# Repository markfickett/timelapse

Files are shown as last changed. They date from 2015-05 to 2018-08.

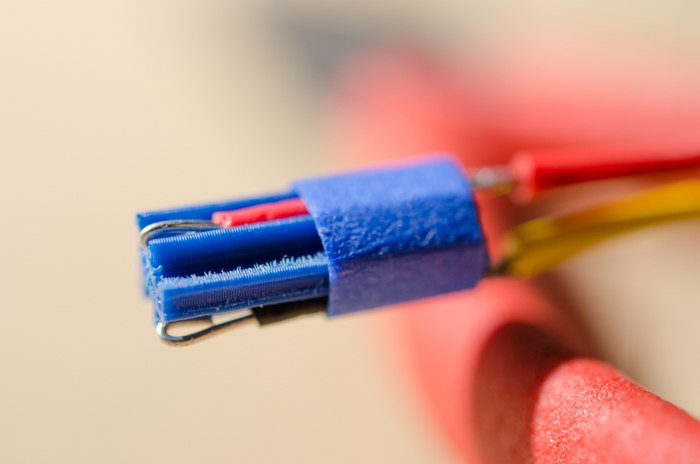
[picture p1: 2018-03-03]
nikond90acplug/151021nikond90acplugendside.jpg

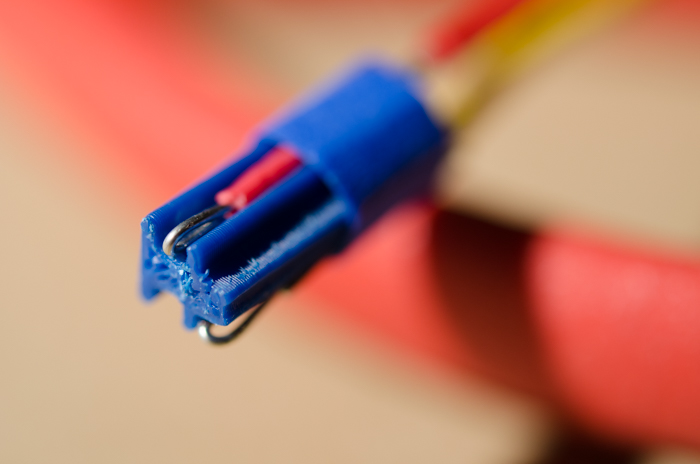
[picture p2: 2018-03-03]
nikond90acplug/151021nikond90acplugendquarter.jpg

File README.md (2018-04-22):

# Outdoor Battery Powered dSLR Time Lapse

## Parts

This is based around a dSLR for the high-quality image sensor and lenses. A Nikon D90 costs around $200 used in 2015, and has connections for a wired remote and external power supply.

### Control board

The control board is Arduino-based, using a bare ATMega328p, with a MOSFET to control camera power and an opto-isolater to control camera exposure.

#### Components

Many of these parts may be found cheaper at Mouser or DigiKey, but SparkFun or Adafruit makes finding the right component and learning to use it easy.

 * ATMega328p [$6 from Sparkfun](https://www.sparkfun.com/products/10524) and 28-DIP socket [$1 from SparkFun](https://www.sparkfun.com/products/7942).
 * optoisolator (2+ channel) [$2 from Mouser](http://www.mouser.com/ProductDetail/Vishay-Semiconductors/ILD2/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)
 * Chrono Dot real time clock module [$20 from Adafruit](https://www.adafruit.com/products/255)
 * MOSFET [$1 from Sparkfun](https://www.sparkfun.com/products/10213) for camera power control
 * NPN transistor [$1 from Sparkfun](https://www.sparkfun.com/products/521) for LED display power control
 * photoresistor (CdS) [$1 from Adafruit](http://www.adafruit.com/product/161), to sense the camera's activity LED and ambient light levels
 * 5V 1A buck converter for regulated power [$15 from Adafruit](https://www.adafruit.com/product/1065). Idle current of under 2mA.
 * Small tactile switches [$5 for 20 from Adafruit](https://www.adafruit.com/product/1489) for a reset and debug buttons.
 * I2C 7-segment display [$20 from Adafruit](https://www.adafruit.com/product/878), though I might go for the [alphanumeric version](https://www.adafruit.com/product/1911) were I starting again.
 * assorted resistors
 * 22 uF electrolytic capacitor for filtering

I used [SparkFun's $20 Tiny AVR Programmer](https://www.sparkfun.com/products/11801) to [upload to the bare ATMega328](https://www.sparkfun.com/products/11801#comment-561f19cbce395f7a0d8b4567). I soldered [female headers](https://www.adafruit.com/product/598) on the programmer, and used Adafruit's [$4 female-female jumpers](https://www.adafruit.com/product/266) along with [extra-long headers](https://www.adafruit.com/product/400) to jump to the ISP header on the board.

#### Circuit

See the `eagle/` subdirectory for circuit and PCB details including [schematic PDF](eagle/timelapse.sch.pdf).

I designed PCBs using EAGLE's non-commercial free license and autolayout, following [SparkFun's tutorial](https://learn.sparkfun.com/tutorials/using-eagle-schematic), and had them printed by [OSH Park](https://oshpark.com/).

### Off-Board Parts and Connectors

 * 12v to 9v DC regulator [$8 on Amazon](http://www.amazon.com/gp/product/B00A71E52G) for power to camera (draws 12mA @ 12v with no load)
 * AC adapter plug (3D printed plug for Nikon D90; [photo](nikond90acplug/151021nikond90acplugendquarter.jpg), [STL file](nikond90acplug/NikonD90AcPlugReducedH.stl), [Thingiverse](https://www.thingiverse.com/thing:1107374/apps/print/))
 * XT60s (power connections, [$2 from Sparkfun](https://www.sparkfun.com/products/10474), compare at HobbyKing)
 * servo cables (peripheral/control connections)
 * lamp cord (battery connection)
 * wired dSLR remote [$6 MC-DC2 clone on Amazon](http://www.amazon.com/gp/product/B003JR8GCU)

### Hardware

A Pelican case provides a sturdy, watertight enclosure which is easy to open and close; and the fins on the hinge side facilitate mounting.

 * Pelican case 1300 NF ($60 on eBay)
 * glass (from a small thrift-store picture frame; attached with JB weld)
 * silica gel (dried and reused)
 * treated wood and screws for mounting
 * 5W solar panel ([$35 on Amazon](https://www.amazon.com/gp/product/B004FOEUI0)) for locations with a fair amount of direct sun, or as overkill, 30W panel ([$60 on Amazon](https://www.amazon.com/gp/product/B00JDRG69K))
 * SLA solar charge controller (this [$10 CMP12 on Amazon](https://www.amazon.com/gp/product/B010FNO9NU) works well, but draws 10mA when idle, even with its indicator LEDs clipped)
 * 12v sealed lead-acid battery (a 4Ah version for home security systems works well; [$20 on Amazon](https://www.amazon.com/dp/B00GYHBACA))

## Related

[Brinno](http://brinno.com/time-lapse-camera/TLC200Pro) makes a 1.3MP HDR timelapse camera with CS-mount lenses and a weatherproof case, claiming 45-day battery life on 4xAA.

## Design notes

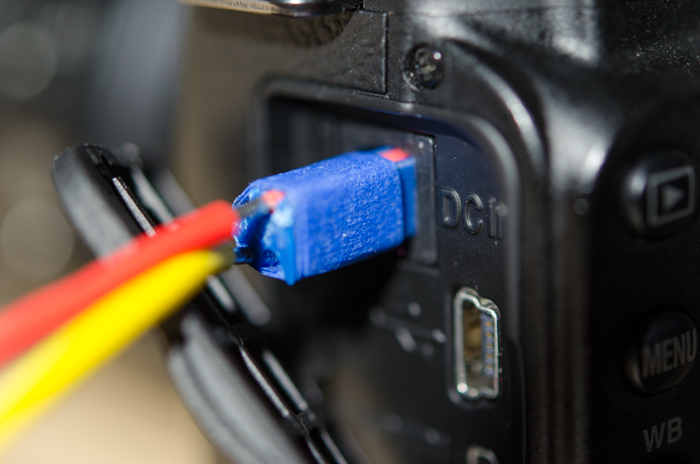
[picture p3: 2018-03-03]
nikond90acplug/151103nikond90acpluginjack.jpg

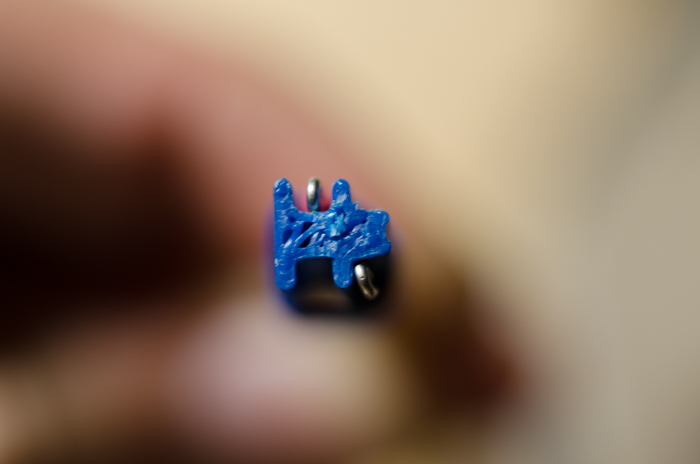
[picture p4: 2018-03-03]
nikond90acplug/151103nikond90acplugend.jpg

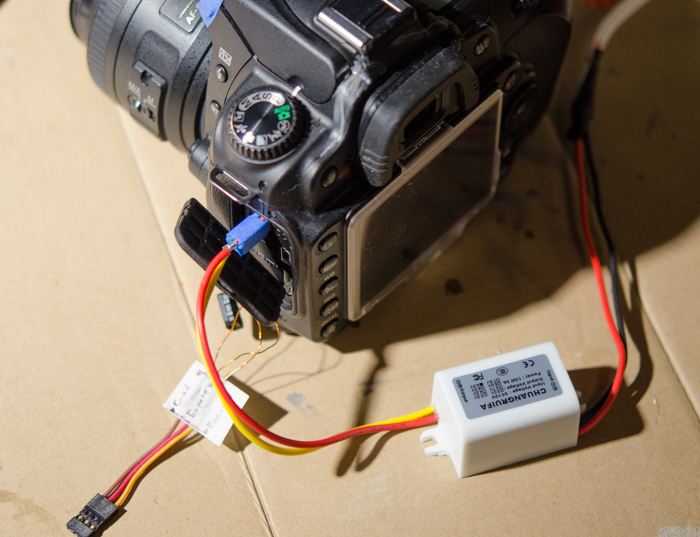
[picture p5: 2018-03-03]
nikond90acplug/151021nikond90acplugincamerafar.jpg

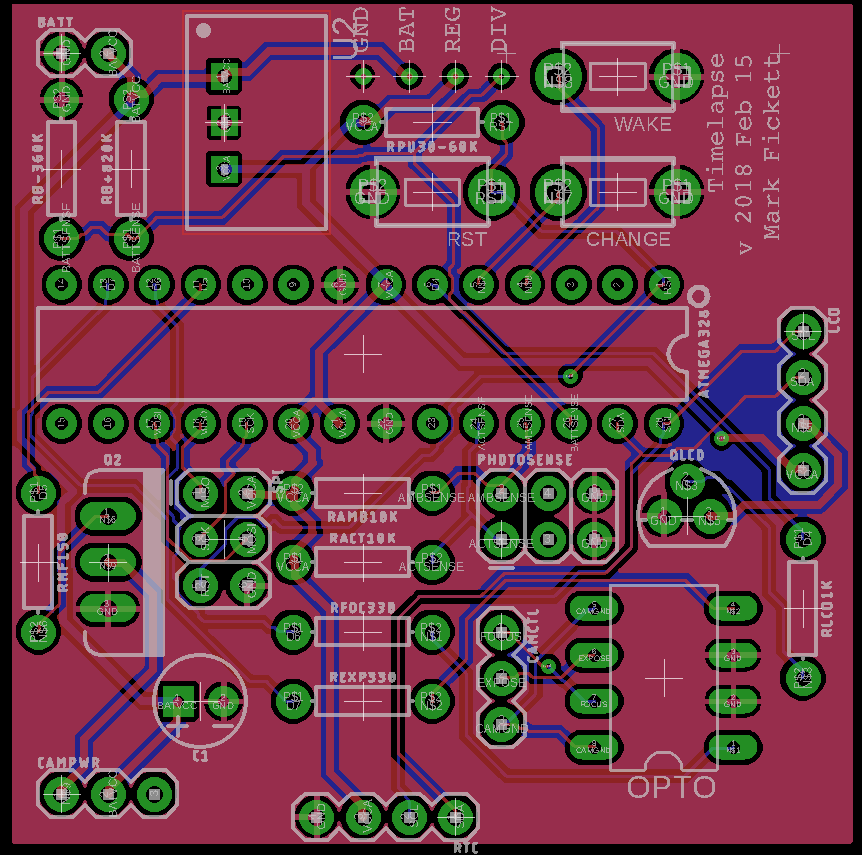
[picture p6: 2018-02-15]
eagle/timelapse.brd.png

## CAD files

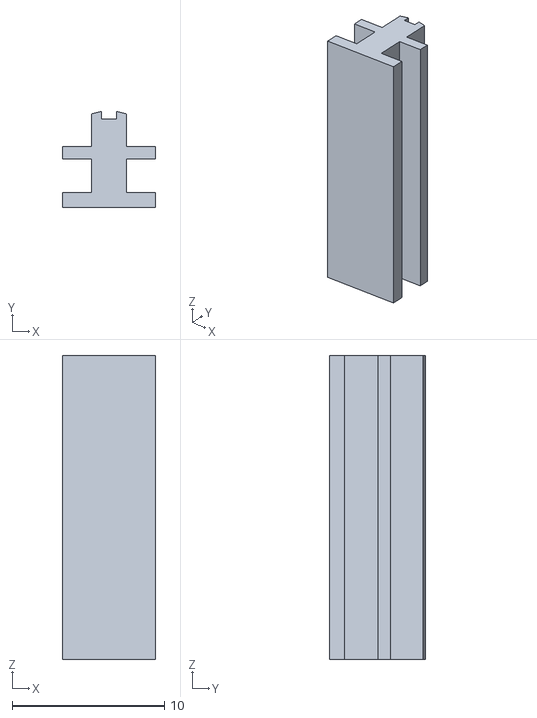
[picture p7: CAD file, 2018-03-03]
nikond90acplug/NikonD90AcPlugReducedH.stl
6.12 x 6.33 x 20.0

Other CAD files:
nikond90acplug/NikonD90AcPlugFootprint.skp
nikond90acplug/NikonD90AcPlugReducedH.skp

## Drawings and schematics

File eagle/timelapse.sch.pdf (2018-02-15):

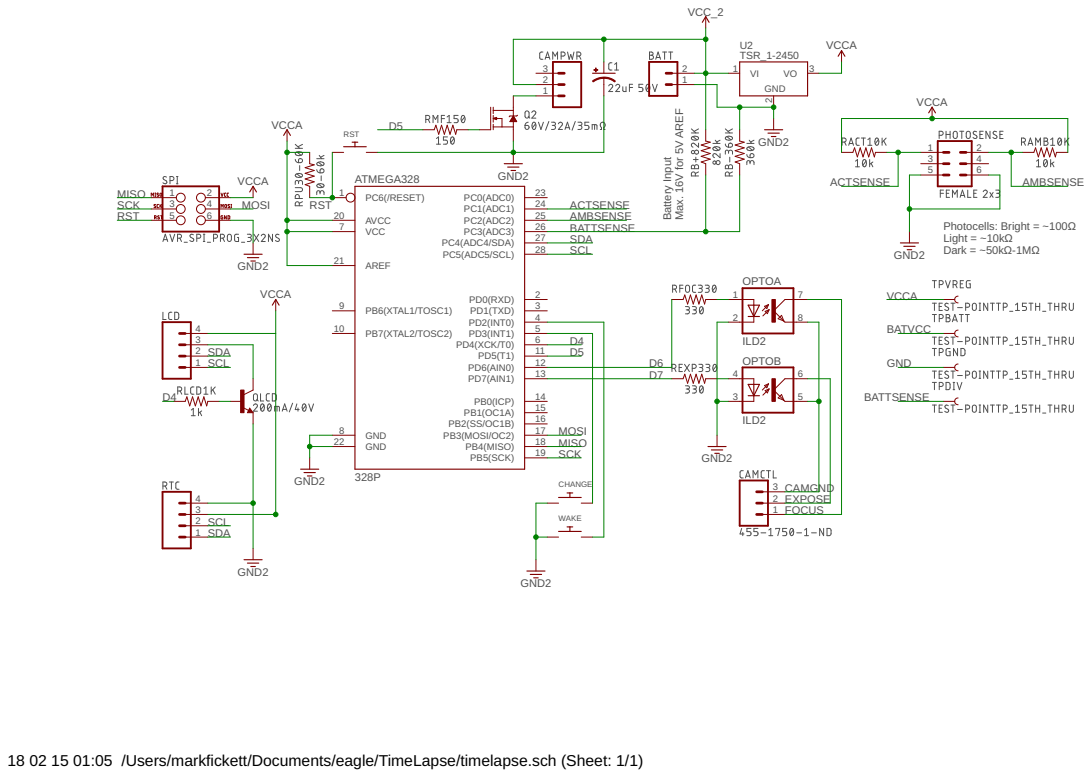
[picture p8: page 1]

22 | MISO

MOSI

18 02 15 01:05 /Users/markfickett/Documents/eagle/TimeLapse/timelapse.sch (Sheet: 1/1)

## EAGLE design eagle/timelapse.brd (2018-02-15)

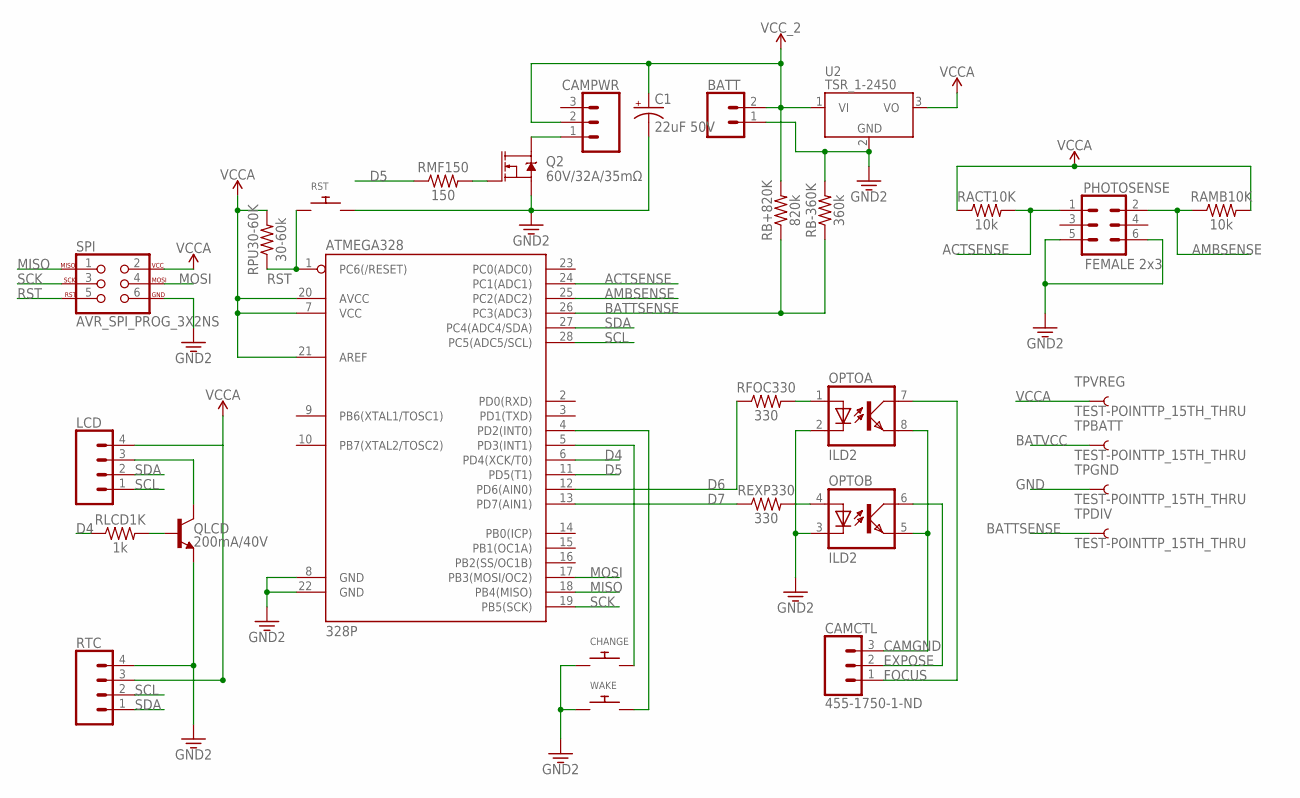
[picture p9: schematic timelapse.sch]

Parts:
ATMEGA328: 328P; DIP28
BATT: CONN_02; 1X02
C1: 22uF 50V; CPOL-RADIAL-2.5MM-5MM
CAMCTL: 455-1750-1-ND; 1X03
CAMPWR: CONN_03; 1X03
CHANGE: SWITCH_PUSHBUTTONEVQ-PE; TACT_PANA-EVQ
LCD: CONN_04; 1X04
OPTO: ILD2; DIL08
PHOTOSENSE: FEMALE 2x3; 2X3
Q2: 60V/32A/35mΩ; TO220V
QLCD: 200mA/40V; TO-92
RACT10K: 10k; AXIAL-0.3
RAMB10K: 10k; AXIAL-0.3
RB+820K: 820k; AXIAL-0.3
RB-360K: 360k; AXIAL-0.3
REXP330: 330; AXIAL-0.3
RFOC330: 330; AXIAL-0.3
RLCD1K: 1k; AXIAL-0.3
RMF150: 150; AXIAL-0.3
RPU30-60K: 30-60k; AXIAL-0.3
RST: SWITCH_PUSHBUTTONEVQ-PE; TACT_PANA-EVQ
RTC: CONN_04; 1X04
SPI: AVR_SPI_PROG_3X2NS; 2X3-NS
TPBATT: TEST-POINTTP_15TH_THRU; TP_15TH
TPDIV: TEST-POINTTP_15TH_THRU; TP_15TH
TPGND: TEST-POINTTP_15TH_THRU; TP_15TH
TPVREG: TEST-POINTTP_15TH_THRU; TP_15TH
U2: TSR_1-2450; TSR-1
WAKE: SWITCH_PUSHBUTTONEVQ-PE; TACT_PANA-EVQ

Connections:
ACTSENSE: ATMEGA328.24 (PC1(ADC1)), PHOTOSENSE.1, RACT10K.P$2 (2)
AMBSENSE: ATMEGA328.25 (PC2(ADC2)), PHOTOSENSE.2, RAMB10K.P$1 (1)
BATTSENSE: ATMEGA328.26 (PC3(ADC3)), RB+820K.P$1 (1), RB-360K.P$1 (1), TPDIV.P$1
BATVCC: BATT.2, C1.1 (+), CAMPWR.2, RB+820K.P$2 (2), TPBATT.P$1, U2.1 (VI)
CAMGND: CAMCTL.3, OPTO.5 (EMIT), OPTO.8 (EMIT)
D4: ATMEGA328.6 (PD4(XCK/T0)), RLCD1K.P$1 (1)
D5: ATMEGA328.11 (PD5(T1)), RMF150.P$1 (1)
D6: ATMEGA328.12 (PD6(AIN0)), RFOC330.P$1 (1)
D7: ATMEGA328.13 (PD7(AIN1)), REXP330.P$1 (1)
EXPOSE: CAMCTL.2, OPTO.6 (COL)
FOCUS: CAMCTL.1, OPTO.7 (COL)
GND: ATMEGA328.8 (GND), ATMEGA328.22 (GND), BATT.1, C1.2 (-), CHANGE.P$1, OPTO.2 (C), OPTO.3 (C), PHOTOSENSE.5, PHOTOSENSE.6, Q2.3 (S), QLCD.1 (E), RB-360K.P$2 (2), RST.P$2, RTC.4, SPI.6, TPGND.P$1, U2.2 (GND), WAKE.P$1
MISO: ATMEGA328.18 (PB4(MISO)), SPI.1
MOSI: ATMEGA328.17 (PB3(MOSI/OC2)), SPI.4
unnamed: OPTO.1 (A), RFOC330.P$2 (2)
unnamed: OPTO.4 (A), REXP330.P$2 (2)
unnamed: QLCD.2 (B), RLCD1K.P$2 (2)
unnamed: LCD.3, QLCD.3 (C)
unnamed: Q2.1 (G), RMF150.P$2 (2)
unnamed: ATMEGA328.5 (PD3(INT1)), CHANGE.P$2
unnamed: ATMEGA328.4 (PD2(INT0)), WAKE.P$2
unnamed: CAMPWR.1, Q2.2 (D)
RST: ATMEGA328.1 (PC6(/RESET)), RPU30-60K.P$1 (1), RST.P$1, SPI.5
SCK: ATMEGA328.19 (PB5(SCK)), SPI.3
SCL: ATMEGA328.28 (PC5(ADC5/SCL)), LCD.1, RTC.2
SDA: ATMEGA328.27 (PC4(ADC4/SDA)), LCD.2, RTC.1
VCCA: ATMEGA328.7 (VCC), ATMEGA328.20 (AVCC), ATMEGA328.21 (AREF), LCD.4, RACT10K.P$1 (1), RAMB10K.P$2 (2), RPU30-60K.P$2 (2), RTC.3, SPI.2, TPVREG.P$1, U2.3 (VO)

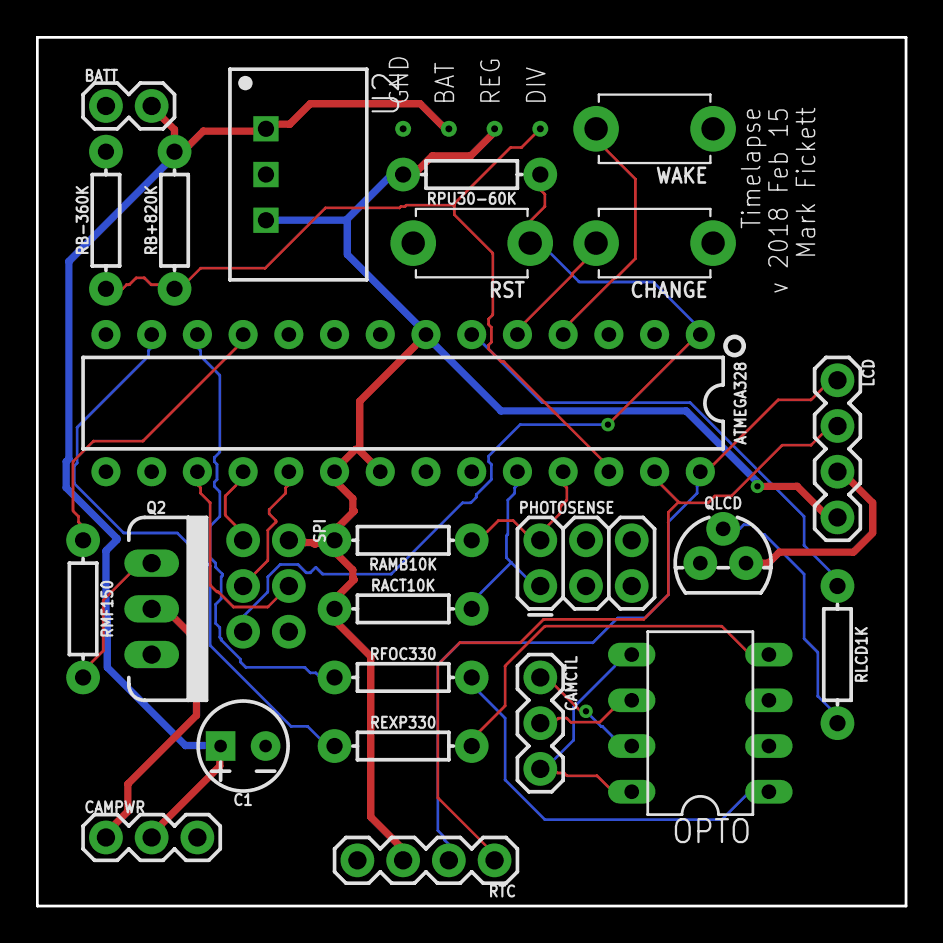
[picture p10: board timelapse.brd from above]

Board: 2 copper layers, 48.3 x 48.3 mm, 29 parts (0 on the bottom side), 27 nets.

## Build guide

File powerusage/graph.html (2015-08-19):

Using Adafruit's INA219B power monitoring breakout board (https://learn.adafruit.com/adafruit-ina219-current-sensor-breakout) to log current drawn by the time lapse controller and camera. The code used is a simplification of their example, logging millis() and ina219.getCurrent_ma() constantly.

Rendered using dygraph (http://dygraphs.com/). Drag and select to zoom in, double-click to zoom back out. Hover over letters on the graph for descriptions.

On this graph: 13.4s spent sleeping or logging, totaling 0.53mAH; and 14.4s spent triggering the camera, totaling 51.1mAH.

Extrapolating: 1 day logging (once every 2s) should consume 57mAH, about the same as taking the exposure. A charge current of 200mA would deliver 100mAH in 30 minutes, allowing for no loss. Or: 1 day taking photos every 10 minutes should consume 7.4AH, which would require 1.5 days of 200mA charging.

Shortening the wait time before and after taking the picture are the clear opportunities for power optimization.

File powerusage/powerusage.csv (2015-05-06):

millis | mA
35500 | 1.60
35503 | 2.20
35505 | 2.00
35508 | 1.50
35511 | 2.00
35513 | 1.60
35516 | 1.80
35519 | 2.20
35521 | 1.90
35524 | 1.60
35527 | 1.70
35529 | 2.00
35532 | 1.40
35534 | 1.10
35537 | 2.20
35540 | 1.40
35543 | 4.30
35546 | 2.00
35549 | 2.00
35551 | 1.80
35554 | 1.90
35556 | 2.10
35559 | 1.80
35562 | 1.80
35564 | 1.80
35567 | 0.40
35570 | 1.80
35572 | 1.90
35575 | 1.70
35577 | 2.00
35580 | 1.10
35584 | 3.70
35586 | 2.20
35589 | 1.50
35592 | 3.90
35594 | 2.00
35597 | 1.90
35599 | 1.90
35602 | 1.80
35605 | 2.00
35607 | 2.00
35610 | 1.70
35612 | 1.80
35615 | 1.80
35618 | 2.40
35620 | 1.60
35623 | 1.20
35627 | 1.90
35629 | 1.60
35632 | 1.00
35634 | 2.20
35637 | 2.00
35640 | 1.50
35642 | 1.90
35645 | 2.20
35648 | 1.90
35650 | 1.60
35653 | 1.80
35655 | 2.00
35658 | 1.50
35661 | 1.80
35663 | 0.10
35666 | 1.80
35670 | 1.60
35672 | 1.30
35675 | 2.00
35678 | 1.60
35680 | 1.00
35683 | 2.20
35685 | 1.70
35688 | 1.30
35691 | 2.00
35693 | 2.00
35696 | 2.70
35698 | 1.50
35701 | 2.00
35704 | 2.30
35706 | 1.50
35709 | 1.80
35713 | -0.30
35715 | 1.90
35718 | 1.50
35720 | 2.10
35723 | 1.80
35726 | 1.80
35728 | 1.50
35731 | 2.20
35734 | 1.70
35736 | 1.00
35739 | 1.30
35741 | 2.40
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

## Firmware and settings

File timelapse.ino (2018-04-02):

/**
 * Run time lapse camera.
 */

#include "Wire.h"
// Using https://github.com/adafruit/RTClib
#include "RTClib.h"
// Adafruit 7-segment LED
#include <Adafruit_GFX.h>
#include "Adafruit_LEDBackpack.h"
// https://github.com/rocketscream/Low-Power
#include "LowPower.h"

#include "config.h"
#include "buttons.h"
#include "schedule.h"

// Chronodot https://www.adafruit.com/products/255 and guide
// learn.adafruit.com/ds1307-real-time-clock-breakout-board-kit/wiring-it-up
// It draws 0.1mA consistently while 3.3 vcc is supplied.
RTC_DS1307 rtc;

// learn.adafruit.com/adafruit-led-backpack/0-dot-56-seven-segment-backpack
Adafruit_7segment display = Adafruit_7segment();

struct EnvironmentData {
  DateTime now;

  int ambientLightLevel; // raw analogRead value
  bool ambientIsLight;

  int vccVoltageReading; // raw analogRead value
  float vccVoltage;

  // from camera activity LED
  int cameraIdleReading; // raw analogRead value
  bool cameraIsIdle;
};

byte charTo7Seg(char c) {
  switch(c) {
    case 'A': return 0b01110111;
    case 'C': return 0b00111001;
    case 'E': return 0b01111001;
    case 'F': return 0b01110001;
    case 'X':
    case 'H': return 0b01110110;
    case 'I': return 0b00110000;
    case 'L': return 0b00111000;
    case 'O': return 0b00111111;
    case 'P': return 0b01110011;
    case 'S': return 0b01101101;
    case 'U': return 0b00111110;
    case 'V': return 0b00111100;
    case 'a': return 0b11011100;
    case 'b': return 0b01111100;
    case 'd': return 0b01011110;
    case 'g': return 0b01101111;
    case 'h': return 0b01110100;
    case 'n': return 0b01010100;
    case 't': return 0b01110000;
    case 'y': return 0b01101110;
    case '.': return 0b10000000;
    case '!': return 0b10000010;
    default:
      return 0b11111111;
  }
}

Schedule schedule;

void setup() {
  // This must be called before analogRead if voltage is applied to the AREF
  // pin, or else the board may be damaged.
  analogReference(EXTERNAL);

  pinMode(PIN_CAMERA_IDLE_SENSE, INPUT);
  pinMode(PIN_AMBIENT_LIGHT_SENSE, INPUT);
  pinMode(PIN_BATTERY_SENSE, INPUT);

  pinMode(PIN_CAMERA_POWER_SUPPLY, OUTPUT);
#ifdef CAMERA_POWER_ALWAYS_ON
  digitalWrite(PIN_CAMERA_POWER_SUPPLY, HIGH);
#else
  digitalWrite(PIN_CAMERA_POWER_SUPPLY, LOW);
#endif

  pinMode(PIN_WAKE_BUTTON, INPUT_PULLUP);
  pinMode(PIN_CHANGE_BUTTON, INPUT_PULLUP);

  pinMode(PIN_CAMERA_FOCUS, OUTPUT);
  digitalWrite(PIN_CAMERA_FOCUS, LOW);
  pinMode(PIN_CAMERA_EXPOSE, OUTPUT);
  digitalWrite(PIN_CAMERA_EXPOSE, LOW);

  pinMode(PIN_7SEG_POWER, OUTPUT);
  digitalWrite(PIN_7SEG_POWER, HIGH);
  delay(50);  // Give it time to wake up.
  display.begin(0x70 /* default I2C address */); // also sets max brightness
  display.clear();
  display.writeDigitRaw(0, charTo7Seg('h'));
  display.writeDigitRaw(1, charTo7Seg('E'));
  display.writeDigitRaw(3, charTo7Seg('L'));
  display.writeDigitRaw(4, charTo7Seg('O') | charTo7Seg('.'));
  display.writeDisplay();
  delay(1000);

  // Real-time clock setup.
  rtc.begin();
  int clockProgress = 0;
  while (!rtc.isrunning()) {
    // It may be necessary to wait, after begin(), before adjust() can be
    // called. Docs on isrunning() are unclear whether it's really the right
    // check.
    display.clear();
    clockProgress = clockProgress + 1 % 5;
    display.writeDigitRaw(clockProgress, charTo7Seg('.'));
    display.writeDisplay();
    delay(100);
  }
  // If the clock's date is set way in the past, it is probably fresh or reset
  // and should be set to the host machine's clock at compile time.
  if (rtc.now().year() < 2018) {
    DateTime now = DateTime(__DATE__, __TIME__); // time at compilation
    now = now + TimeSpan(0, 5, 0, 0); // EDT => UTC
    rtc.adjust(now);
  }

  attachInterrupt(
      digitalPinToInterrupt(PIN_WAKE_BUTTON), handleWakePress, FALLING);
  attachInterrupt(
      digitalPinToInterrupt(PIN_CHANGE_BUTTON), handleChangePress, FALLING);
}

struct EnvironmentData getEnvironmentData() {
  struct EnvironmentData data;
  data.now = rtc.now();
  data.ambientLightLevel = analogRead(PIN_AMBIENT_LIGHT_SENSE);
  data.ambientIsLight = data.ambientLightLevel < AMBIENT_LIGHT_LEVEL_DARK;
  data.vccVoltageReading = analogRead(PIN_BATTERY_SENSE);
  data.vccVoltage =
      // Convert reading to sensed voltage.
      (data.vccVoltageReading / 1023.0) * AREF
      // Scale sensed voltage to actual Vcc based on dividers.
      * VCC_DIVIDER_ADJ * (VCC_DIVIDER_SRC + VCC_DIVIDER_GND) / VCC_DIVIDER_GND;
  data.cameraIdleReading = analogRead(PIN_CAMERA_IDLE_SENSE);
  data.cameraIsIdle = data.cameraIdleReading >= CAMERA_IDLE_THRESHOLD;
  return data;
}

void displayTime(int hours, int minutes, bool drawColon) {
  display.clear();
  display.writeDigitNum(0, hours / 10);
  display.writeDigitNum(1, hours % 10);
  display.drawColon(drawColon);
  display.writeDigitNum(3, minutes / 10);
  display.writeDigitNum(4, minutes % 10);
  display.writeDisplay();
}

void debugMode() {
  struct EnvironmentData data = getEnvironmentData();
  consumeChangePress();  // clear any old presses

  // Schedule / next photo
  while (!consumeWakePress()) {
    data = getEnvironmentData();
    TimeSpan remaining = schedule.next - data.now;

    // current interval
    display.clear();
    switch(schedule.period) {
      case ONE_MINUTE: // :01
        display.drawColon(true);
        display.writeDigitNum(3, 0);
        display.writeDigitNum(4, 1);
        break;
      case TEN_MINUTES: // :10
        display.writeDigitNum(3, 1);
        display.writeDigitNum(4, 0);
        display.drawColon(true);
        break;
      case ONE_HOUR: // 1h
        display.writeDigitNum(0, 1);
        display.writeDigitRaw(1, charTo7Seg('h'));
        break;
      case ONE_DAY: // 1d
        display.writeDigitNum(0, 1);
        display.writeDigitRaw(1, charTo7Seg('d'));
        break;
    }
    display.writeDisplay();
    delay(500);

    // Is it still SCHEduled for the future, or are we PAST the schedule time?
    display.clear();
    if (remaining.totalseconds() >= 0) {
      display.writeDigitRaw(0, charTo7Seg('S'));
      display.writeDigitRaw(1, charTo7Seg('C'));
      display.writeDigitRaw(3, charTo7Seg('H'));
      display.writeDigitRaw(4, charTo7Seg('E'));
    } else {
      display.writeDigitRaw(0, charTo7Seg('P'));
      display.writeDigitRaw(1, charTo7Seg('A'));
      display.writeDigitRaw(3, charTo7Seg('S'));
      display.writeDigitRaw(4, charTo7Seg('t'));
    }
    display.writeDisplay();
    delay(500);

    // time remaining/elapsed (absolute value)
    if (remaining.totalseconds() < 0) {
      remaining = TimeSpan(-remaining.totalseconds());
    }
    display.clear();
    if (remaining.totalseconds() <= 60) {
      display.println(remaining.totalseconds());
    } else if (remaining.days() <= 2) {
      displayTime(
          remaining.hours() + remaining.days() * 24,
          remaining.minutes(),
          true /* drawColon */);
    } else {
      display.println(remaining.days() * 10);
      display.writeDigitRaw(4, charTo7Seg('d'));
    }
    display.writeDisplay();
    delay(1000);

    if (consumeChangePress()) {
      schedule.cyclePeriodAndRescheduleAfter(schedule.getLastPhotoTime());
    }
  }

  // time, UTC
  bool colonBlink = false;
  while (!consumeWakePress()) {
    displayTime(data.now.hour(), data.now.minute(), colonBlink = !colonBlink);
    delay(1000);
    data = getEnvironmentData();
  }

  // VCC (battery voltage)
  while (!consumeWakePress()) {
    display.clear();
    display.writeDigitRaw(0, charTo7Seg('V'));
    display.writeDigitRaw(1, charTo7Seg('C'));
    display.writeDigitRaw(3, charTo7Seg('C'));
    display.writeDisplay();
    delay(500);
    display.clear();
    display.println(data.vccVoltage);
    display.writeDisplay();
    delay(1000);
    display.clear();
    display.println(data.vccVoltageReading);
    display.writeDisplay();
    delay(1000);
    data = getEnvironmentData();
  }

  // take a picture
  while (!consumeWakePress()) {
    display.clear();
    display.writeDigitRaw(0, charTo7Seg('P'));
    display.writeDigitRaw(1, charTo7Seg('I'));
    display.writeDigitRaw(3, charTo7Seg('C'));
    display.writeDisplay();
    if (consumeChangePress()) {
      schedule.recordLastPhoto(data.now);
      takePicture();
      schedule.advancePast(data.now);
    }
    delay(50);
  }

#ifndef CAMERA_POWER_ALWAYS_ON
  // camera power on/off
  bool isOn = false;
  while (!consumeWakePress()) {
    display.clear();
    if (isOn) {
      display.writeDigitRaw(0, charTo7Seg('O'));
      display.writeDigitRaw(1, charTo7Seg('n'));
    } else {
      display.writeDigitRaw(0, charTo7Seg('O'));
      display.writeDigitRaw(1, charTo7Seg('F'));
      display.writeDigitRaw(3, charTo7Seg('F'));
    }
    display.writeDisplay();
    if (consumeChangePress()) {
      isOn = !isOn;
      digitalWrite(PIN_CAMERA_POWER_SUPPLY, isOn ? HIGH : LOW);
    }
    delay(50);
  }
  digitalWrite(PIN_CAMERA_POWER_SUPPLY, LOW);
#endif CAMERA_POWER_ALWAYS_ON

  // ambient light level
  while (!consumeWakePress()) {
    display.clear();
    display.writeDigitRaw(0, charTo7Seg('L'));
    display.writeDigitRaw(1, charTo7Seg('I'));
    display.writeDigitRaw(3, charTo7Seg('g'));
    display.writeDigitRaw(4, charTo7Seg('h'));
    display.writeDisplay();
    delay(500);
    displayThreshold(data.ambientIsLight, data.ambientLightLevel);
    data = getEnvironmentData();
  }

  // camera activity LED
  while (!consumeWakePress()) {
    display.clear();
    display.writeDigitRaw(0, charTo7Seg('I'));
    display.writeDigitRaw(1, charTo7Seg('d'));
    display.writeDigitRaw(3, charTo7Seg('L'));
    display.writeDigitRaw(4, charTo7Seg('E'));
    display.writeDisplay();
    delay(500);
    displayThreshold(data.cameraIsIdle, data.cameraIdleReading);
    data = getEnvironmentData();
  }

  display.clear();
  display.writeDigitRaw(0, charTo7Seg('b'));
  display.writeDigitRaw(1, charTo7Seg('y'));
  display.writeDigitRaw(3, charTo7Seg('E'));
  display.writeDigitRaw(4, charTo7Seg('!'));
  display.writeDisplay();
  delay(500);
  for(int brightness = 15; brightness >= 0; brightness--) {
    delay(100);
    display.setBrightness(brightness);
  }
  display.clear();
  display.writeDisplay();
  display.setBrightness(15);
  consumeWakePress();  // clear any stray presses again
  consumeChangePress();
}

void displayThreshold(bool meetsThreshold, int analogValue) {
  display.clear();
  if (meetsThreshold) {
    display.writeDigitRaw(0, charTo7Seg('y'));
    display.writeDigitRaw(1, charTo7Seg('E'));
    display.writeDigitRaw(3, charTo7Seg('S'));
  } else {
    display.writeDigitRaw(1, charTo7Seg('n'));
    display.writeDigitRaw(3, charTo7Seg('O'));
  }
  display.writeDisplay();
  delay(500);
  display.clear();
  display.println(analogValue);
  display.writeDisplay();
  delay(1000);
}

void takePicture() {
  display.clear();
  display.writeDigitRaw(0, charTo7Seg('E'));
  display.writeDigitRaw(1, charTo7Seg('X'));
  display.writeDigitRaw(3, charTo7Seg('P'));
  display.writeDisplay();

#ifndef CAMERA_POWER_ALWAYS_ON
  digitalWrite(PIN_CAMERA_POWER_SUPPLY, HIGH);
  waitForCameraActivity();
#endif

  digitalWrite(PIN_CAMERA_FOCUS, HIGH);
  digitalWrite(PIN_CAMERA_EXPOSE, HIGH);
  delay(CAMERA_EXPOSE_TIME_MS);
  digitalWrite(PIN_CAMERA_FOCUS, LOW);
  digitalWrite(PIN_CAMERA_EXPOSE, LOW);

  waitForCameraActivity();

#ifndef CAMERA_POWER_ALWAYS_ON
  digitalWrite(PIN_CAMERA_POWER_SUPPLY, LOW);
#endif
  display.clear();
  display.writeDisplay();
}

void waitForCameraActivity() {
  struct EnvironmentData data = getEnvironmentData();
  int checkCount = 0;
  // Wait for the activity light to come on...
  while (data.cameraIsIdle && checkCount++ < CAMERA_FAILSAFE_WAIT_COUNT_LIMIT) {
    delay(CAMERA_ACCESS_WAIT_INTERVAL_MS);
    data = getEnvironmentData();
  }
  checkCount = 0;
  int idleCycles = 0;
  // ...and then to stay off.
  while (idleCycles < 4 && checkCount++ < CAMERA_FAILSAFE_WAIT_COUNT_LIMIT) {
    if (data.cameraIsIdle) {
      idleCycles++;
    }
    delay(CAMERA_ACCESS_WAIT_INTERVAL_MS);
    data = getEnvironmentData();
  }
}

void loop() {
  if (consumeWakePress()) {
    debugMode();
  }

  struct EnvironmentData data = getEnvironmentData();
  if (data.vccVoltage >= VCC_VOLTAGE_LOW
      && data.ambientIsLight
      && schedule.isTimeFor(data.now)) {
    // Record the last photo time before taking it in case of brown-outs.
    schedule.recordLastPhoto(data.now);
    takePicture();
    schedule.advancePast(data.now);
  }

  lowPowerSleep();
}

void lowPowerSleep() {
  display.clear();
  display.writeDisplay();
  display.setBrightness(0);
  digitalWrite(PIN_7SEG_POWER, LOW);

  // During power-down, the "wake" button interrupt will be registered, and will
  // immediately cancel power-down mode.
  // With adafru.it/1065 step-down transformer (6.5-32v in, 5v out), the board
  // draws 1.3mA asleep. (The power regulator draws 1-2mA, so accounts for most
  // if not all of this.)
  LowPower.powerDown(SLEEP_8S, ADC_OFF, BOD_ON);

  digitalWrite(PIN_7SEG_POWER, HIGH);
  // Give the display time to wake up. Without an explicit delay, it takes
  // 2-4s to reconnect [retries/backoff?].
  delay(50);
  // Must call begin() again after power cycling the display.
  display.begin(0x70 /* default I2C address */); // also sets max brightness
}

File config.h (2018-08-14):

#pragma once
/**
 * Pin-number and behavior configuration.
 */

// Leave the camera on all the time. When a Nikon D90 is power cycled (w/o its
// own battery and with the power switch in the "on" position) it starts a new
// folder for every photo and resets settings (like noise reduction).
// #define CAMERA_POWER_ALWAYS_ON

// This value is passed to Narcoleptic as an int, so must be < INT_MAX (32767).
#define SLEEP_INTERVAL_MILLIS (10 * 1000)

// 12v (battery) power supply for the 9V regulator powering the camera.
#define PIN_CAMERA_POWER_SUPPLY 5

// To camera via opto-isolator.
#define PIN_CAMERA_FOCUS 6
#define PIN_CAMERA_EXPOSE 7

// Sense the memory-access LED on the camera to detect when an exposure is done
// and written to storage.
#define PIN_CAMERA_IDLE_SENSE A1
// Threshold for the analog reading for the camera memory-access LED. LED off
// (done/idle) is around 900+, on (active) is lower.
#define CAMERA_IDLE_THRESHOLD 900
// How long to wait between each time checking if the camera is done taking
// the exposure.
#define CAMERA_ACCESS_WAIT_INTERVAL_MS 50
// Number of times to repeat waiting for the camera to be done taking the
// exposure (1 minute). Also used waiting for startup.
#define CAMERA_FAILSAFE_WAIT_COUNT_LIMIT 1200
// Duration to 'press' the shutter switch.
#define CAMERA_EXPOSE_TIME_MS 100

// 500 = normal room, 900 = dim, 950+ = dark
#define PIN_AMBIENT_LIGHT_SENSE A2
#define AMBIENT_LIGHT_LEVEL_DARK 950

#define PIN_BATTERY_SENSE A3
// nominally 5v
#define AREF 4.984

// 11.8v is generally considered a lower limit for safe SLA discharge. Allow a
// little buffer, since we want to keep logging even if battery voltage is too
// low to take photos. solarnavigator.net/battery_charging.htm
#define VCC_VOLTAGE_LOW 11.8

// Resistor values for battery. Each pair may be scaled together arbitrarily
// (ex: 4.7 and 1.2 or 47.0 and 12.0). Keep these as floats, for arithematic.
#define VCC_DIVIDER_SRC 838.0
#define VCC_DIVIDER_GND 332.0
// Adjustment factor for the (src + gnd)/gnd factor, to bring observed
// voltages in line with actual voltage.
#define VCC_DIVIDER_ADJ 1.026
// Max tolerable Vcc = 17.6v =
//     AREF * (VCC_DIVIDER_SRC + VCC_DIVIDER_GND) / VCC_DIVIDER_GND

#define PIN_WAKE_BUTTON 2
#define PIN_CHANGE_BUTTON 3

#define PIN_7SEG_POWER 4

#define BUTTON_DEBOUNCE_MILLIS 500

// 16:00 eastern during the winter => 21:00 UTC
#define DAILY_HOUR_OF_DAY_UTC 21

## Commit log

2015-04-26 Read temperature and humidity and log to serial.
2015-04-26 Read RTC time and operate camera.
2015-04-27 Log unregulated supply voltage.
2015-04-29 Fix typo in battery voltage computation comment.
    [timelapse.ino]
2015-05-02 Add second voltage input, pull out voltage printer helper function.
2015-05-02 Add current-drawn note for DHT22.
2015-05-02 Add note on uSD card current draw.
2015-05-03 Switch to keep the target photo time on a regular interval. Add low-power sleep using Narcoleptic.
2015-05-05 Fix extra newline in csv.
    [timelapse.ino]
2015-05-05 Update logs combiner with new voltage divider values, status printing; update graph to use subdir.
2015-05-06 Add note about SanDisk 4GB card current.
2015-05-06 Add more power notes. Add comment about using Narcoleptic.millis() in DHT22.
2015-05-06 Add power usage log and graph with annotations.
    [powerusage.csv]
2015-05-06 Annotate unknown power usage point, adjust descriptions.
2015-05-06 Add script to sum power usage.
2015-08-19 Add note for hovering over markers on power graph.
2015-08-20 Adjust voltage divider constants.
2015-08-25 Make the switch to keep the camera on a toggle. Add switching between slow and fast picture-taking rates.
2015-08-25 Fill in current usage while taking a photo in the overview doc.
2015-08-25 Re-expand labels in data printing.
2015-08-25 Print message when done waiting.
2015-08-25 Revert fast-mode duration to omit arithematic.
    [timelapse.ino]
2015-08-30 Switch to PIN_DHT22 for conformity.
2015-08-30 Add status LED with signaling for short / fast modes. Remove frequent debug printing of next scheduled time.
    [timelapse.ino]
2015-08-30 Add a sensor for the camera memory-access LED, and wait for power-on and photo-write instead of hardcoding timings.
2015-08-30 Shorten duration waiting while camera is on.
    [timelapse.ino]
2015-09-29 Switch fast mode versus schedule mode to a #define. Doc dependency sources.
2016-06-30 Fix up incorrectly recorded negative temperatures from DHT22 library in combinelogs.
2016-07-27 Do not halt for SD card error.
    [timelapse.ino]
2016-07-27 Schedule fast-mode photos on round 10-minute marks. Only take fast-mode photos when PV and battery voltage are sufficiently high.
2016-07-28 Turn off reading PV voltage.
2016-07-30 Add note on battery voltage threshold.
2018-02-04 Add README for first version hardware with Arduino Pro.
2018-02-04 Remove voltage / temperature logs.
2018-02-10 Add skeleton of using 7 segment LED and LowPower, initializing new pins.
2018-02-11 Fix Vcc: floats in divider arithematic, print analog reading, adjust actual AREF, restructure equation for clarity.
    [config.h, timelapse.ino]
2018-02-11 Add eagle subdirectory with schema and board layout.
    [timelapse.brd, timelapse.sch, timelapse2routing.brd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]
2018-02-11 Remove old EAGLE files, fix missing wires in schema and add test points.
    [timelapse.brd, timelapse.sch, timelapse2routing.brd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]
2018-02-11 Split button-press handling into separate file.
2018-02-13 Sense camera activity, run power/shutter.
2018-02-14 Add camera power on/off debug item.
2018-02-15 Add correcting factor to voltage divide for vcc.
    [config.h, timelapse.ino]
2018-02-15 Add capacitor for camera power supply.
    [timelapse.brd, timelapse.sch]
2018-03-03 Add SketchUp and STL files for Nikon AC plug.
    [NikonD90AcJackOutline.skp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]
2018-03-03 Remove extra Nikon AC plug files.
    [NikonD90AcJackOutline.skp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]
2018-03-31 no-load current note for 9v regulator
2018-04-02 Add CAMERA_POWER_ALWAYS_ON macro to work around camera internal battery depleting / settings resetting.
    [config.h, timelapse.ino]
2018-08-14 Add script to flatten camera-output directories.
2019-03-07 Switch flattendirs script to python3 explicitly.

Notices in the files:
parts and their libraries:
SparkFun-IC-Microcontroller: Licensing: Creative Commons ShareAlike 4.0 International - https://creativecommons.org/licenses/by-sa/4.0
